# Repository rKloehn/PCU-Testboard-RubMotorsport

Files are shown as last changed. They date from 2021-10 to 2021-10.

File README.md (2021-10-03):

# PCU-Testboard-RubMotorsport

## Overview
The Powertrain Control Board test board (PCU test board for short) was developed in 2020 for the Drivetrain assembly in order to test the functions for the pneumatic switching and coupling of the RUB20 in advance. For this reason, the board contains all the necessary peripherals and connections required for the switching and coupling of the RUB20. The board is supplied with a 12V power supply (like the real PCU in the vehicle). On the board there are connections for two 24V solenoid valves and one proportional valve. Furthermore two sensors with 5V supply voltage each can be connected and the current value of the proportional valve can be read out. For testing the functionality of the switching and coupling process, three push buttons and an adjustment potentiometer are available. All mentioned components were fixed on the board. The control and regulation tasks are performed by a STM32F405RG. The microcontroller can be programmed via the SWD interface on the board. 
<p align="center">
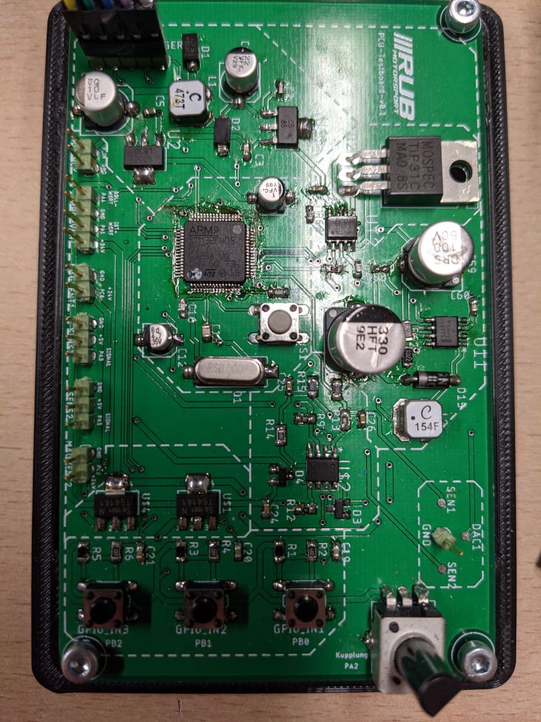
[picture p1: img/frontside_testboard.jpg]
	
</p>

### Sensors
The drivetrain assembly has two sensors specified, which are required for a displacement control of the clutch. A Hall displacement transducer and a pressure sensor are used. The Hall displacement sensor is from the Novotechnik and is sponsored. The sensor is the TFD-4000 series (data sheet TDF-4000). The exact designation of the ordered sensor is: TFD-4021-624-211-401. This sensor has a measuring range of 24mm and a supply voltage of 5V (4.5...5V). The output signal is in the range of 0.25...4.75V and behaves ratiometrically to Ub. The characteristic curve is rising and the sensor is single-channel. Further characteristics can be taken from the data sheet. It is purchased from the company ADZ Nagano. The pressure sensor has a measurable pressure range of FILL IN DATA HERE and requires a supply voltage of 5V. The output signal, similar to the displacement sensor, is ratiometric and is in the range 0.5...4.5V. The sensor has three conductors and a rising characteristic. Further data can be taken from the data sheet (data sheet ADZ-SME).
<p align="center">
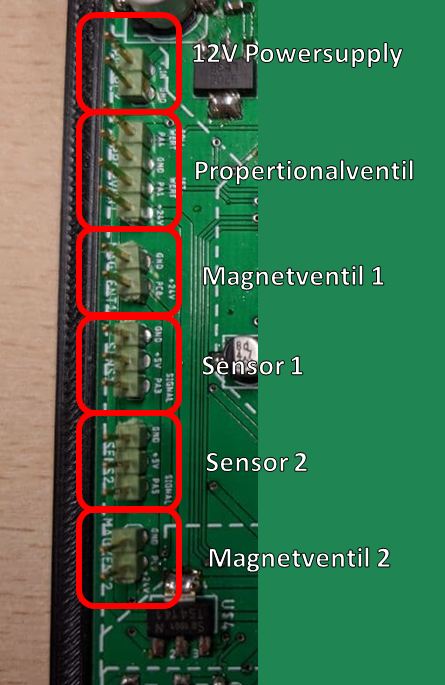
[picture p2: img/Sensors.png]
	
</p>

### Actuators
The actuator system to be controlled by the test board consists of two 24V solenoid valves and one proportional valve. The 24V solenoid valves are from the company FESTO and have the following type description: VUVG-L10-P53E-T-M5_1P3. These are 5/3 [exhausted] valves with a switch-on time of 10ms, a switch-off time of 30ms and a switch-over time of 16ms. The coil is operated with 24V DC with 1W. Further values can be taken from the data sheet (data sheet solenoid valve). The proportional valve is also from the company FESTO and has the type description: VEAA-L-3-D11-Q4-A4-1-R1. The flow valve is controlled by setting the current from 4-20mA. The operating voltage is 24V DC and the electrical connection is a 4-pin M8 connector. Further data can be found in the data sheet.

### User interface
The aim of the test board is to check whether the intended path control and control of the circuit/clutch works. In order for this to happen early in the development process, the board must function completely independently of other boards (e.g. power supply board) or the steering wheel. Thus, it is necessary that the user has a possibility to simulate the actuation of the clutch or the start of a shifting process. For this reason, there are three push buttons on the board, two buttons for upshifting and downshifting and one button for venting the system at the push of a button. A rotary potentiometer also allows the on/off coupling of the motor gearbox. For programming, as mentioned above, the SWD interface is available to the user. The push buttons are all debounced with a corresponding circuit on the board. 

<p align="center">
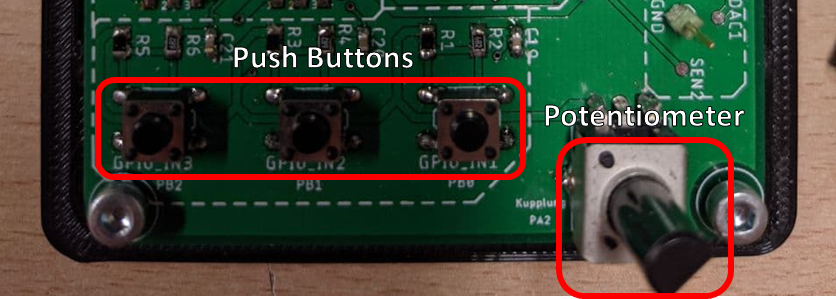
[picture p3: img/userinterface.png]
	
</p>

### Power supply
Several circuits are required for the power supply of the board. In total, exactly three voltage levels are available on the entire PCU test board. The input voltage of the board is 12V DC, which can be provided by a battery or power supply unit. The required current ranges from 0.1A to 0.3A, depending on which peripherals are used. The first voltage level of 5V is achieved by a UA78M05CDCY stepdown converter. The 5V voltage is then either used by the sensors or forms the input voltage for the 5V-3.3V voltage converter. Here a LM2937IMP is used. The 3.3V voltage circuit provides the supply voltage for the microcontroller. The 24V voltage circuit is realized by a StepUp circuit with the MC33063ADG. The 24V are used for the two valves.

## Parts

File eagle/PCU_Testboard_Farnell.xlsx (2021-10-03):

Part Number | Quantity | Description
2146610 | 15 | 100nF 0603
1834255 | 1 | 10µF AlCo 153 CLV 0806
2346907 | 5 | 330nF 0603 50V
2672161 | 5 | 2.2µF 0603 50V
2522596 | 5 | 10000pF 0603 50V
1865475 | 5 | 20pF 0603 50V
2522594 | 5 | 0.1µF 0603 50V
1865487 | 5 | 1500pF 0603 50V
1539494 | 5 | 22µF 0505 35V
1187018 | 5 | 4.7µF 0405 35V
1244367 | 5 | 1µF 0405 25V
2811476 | 5 | 100µF 0810 50V
1299278 | 5 | SK36SMA
2677648 | 5 | SMAJ22
9843671 | 5 | BAS31
1843714 | 5 | 1N5819-B
1829495 | 10 | B3F-1022
2063972 | 1 | FOXSDLF
1652993 | 5 | 39k 0805
1577671 | 5 | 6.8k 0805
2483951 | 5 | 10k 0805
2469524 | 2 | 10k Potentiometer PTV09A-4020F-B103
9294341 | 2 | TIP31C
2215477 | 5 | BTS4141N
1332118 | 5 | MCP6002-E/SN
2296030 | 5 | UA78M05CDCY
3122675 | 5 | LM2937IMP-3.3/NOPB
9664440 | 2 | MC33063ADG
2312176 | 10 | 165 0805
2073658 | 10 | 1.7k 0805
1469911 | 10 | 3.3k 0805
8067600 | 10 | 0.22 0603
1653073 | 10 | 180 0603
1739017 | 10 | 2.2k 0603
2331534 | 10 | 47k 0603
2059432 | 10 | 20k 0603
1692517 | 10 | 100k 0603
2408293 | 2 | 47µH
2408300 | 2 | 150µH LPS6235
1022256 | 10 | Pin8
1868428 | 2 | 330µF 1010

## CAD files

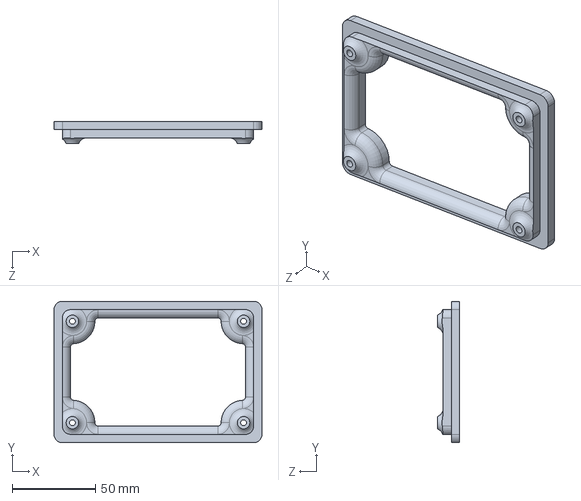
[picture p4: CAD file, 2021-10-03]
eagle/PCU_Testboard_Stand.SLDPRT
125.0 x 85.0 x 13.5 mm

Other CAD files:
eagle/PCU_Testboard_Stand.STL

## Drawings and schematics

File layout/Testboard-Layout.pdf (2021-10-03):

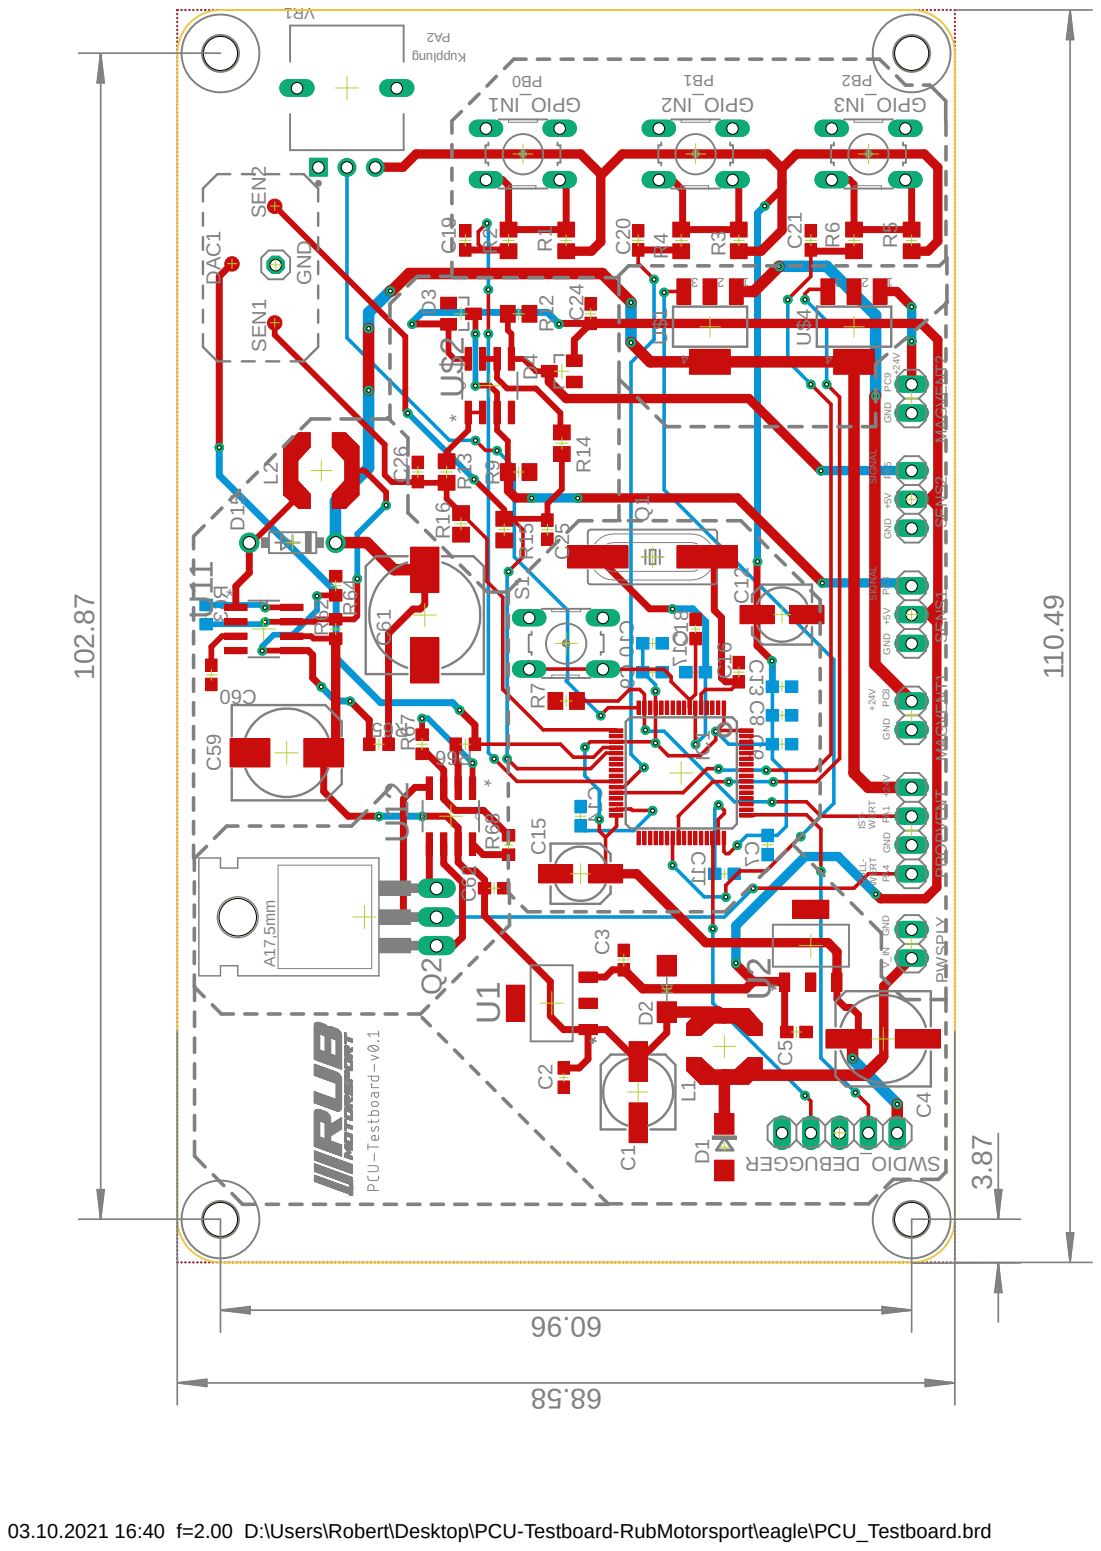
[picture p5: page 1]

* GND V_IN SOLL- WERT GND IST- WERT +24V GND +24V GND GND GND +5V +5V SIGNAL SIGNAL +24V

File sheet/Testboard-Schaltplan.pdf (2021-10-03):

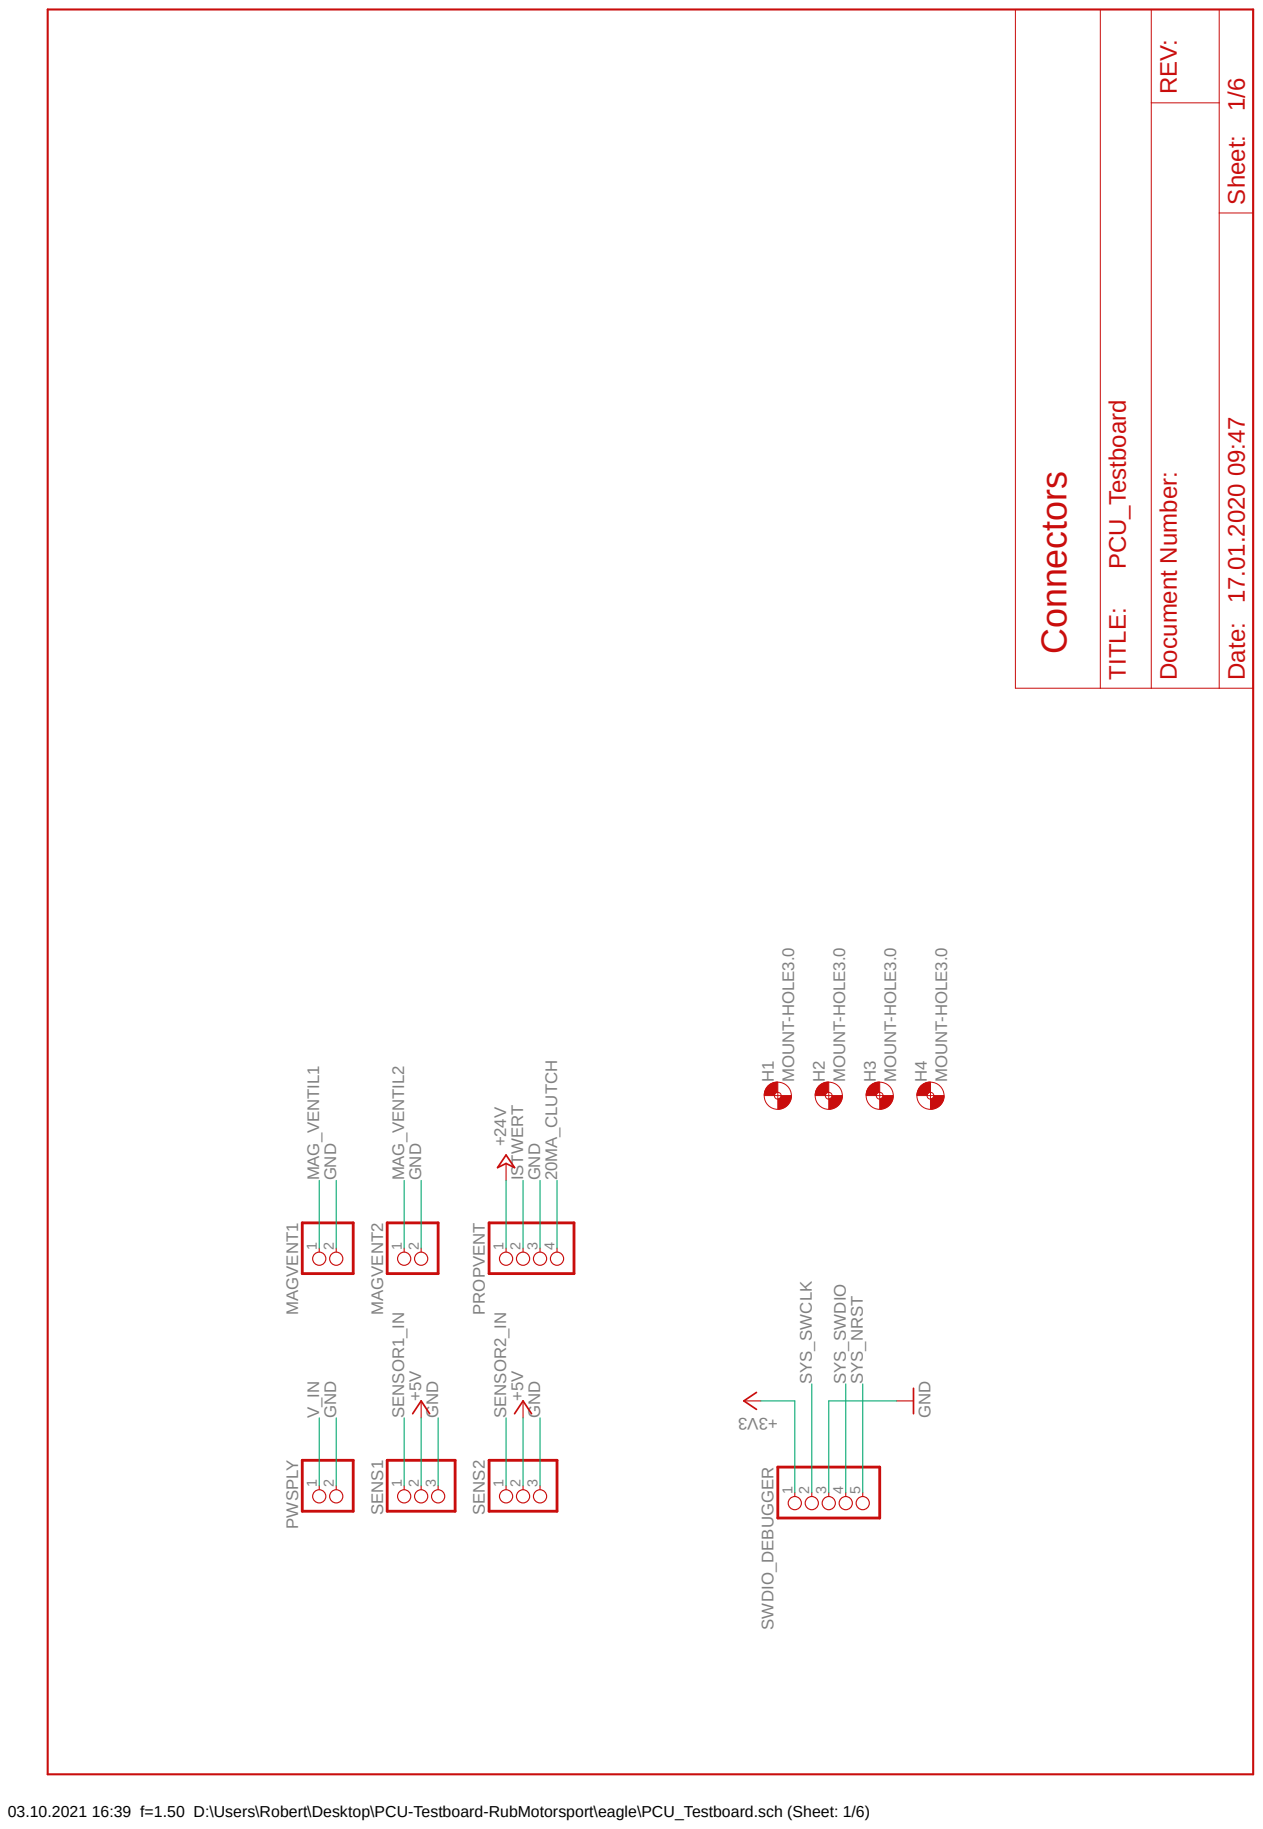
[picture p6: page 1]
5 SWDIO_DEBUGGER1; 2 PWSPLY 1; 3 SENS1; 2 MAGVENT1 1; 2 MAGVENT2; 3 SENS2

4 PROPVENT H1 H2 H3 H4 SYS_SWCLK SYS_SWDIO SYS_NRST GND GND GND GND GND GND V_IN MAG_VENTIL1 MAG_VENTIL2 ISTWERT SENSOR1_IN SENSOR2_IN 20MA_CLUTCH Connectors Date: Sheet: REV: TITLE: Document Number: 17.01.2020 09:47 1/6 PCU_Testboard

03.10.2021 16:39 f=1.50 D:\Users\Robert\Desktop\PCU-Testboard-RubMotorsport\eagle\PCU_Testboard.sch (Sheet: 1/6)

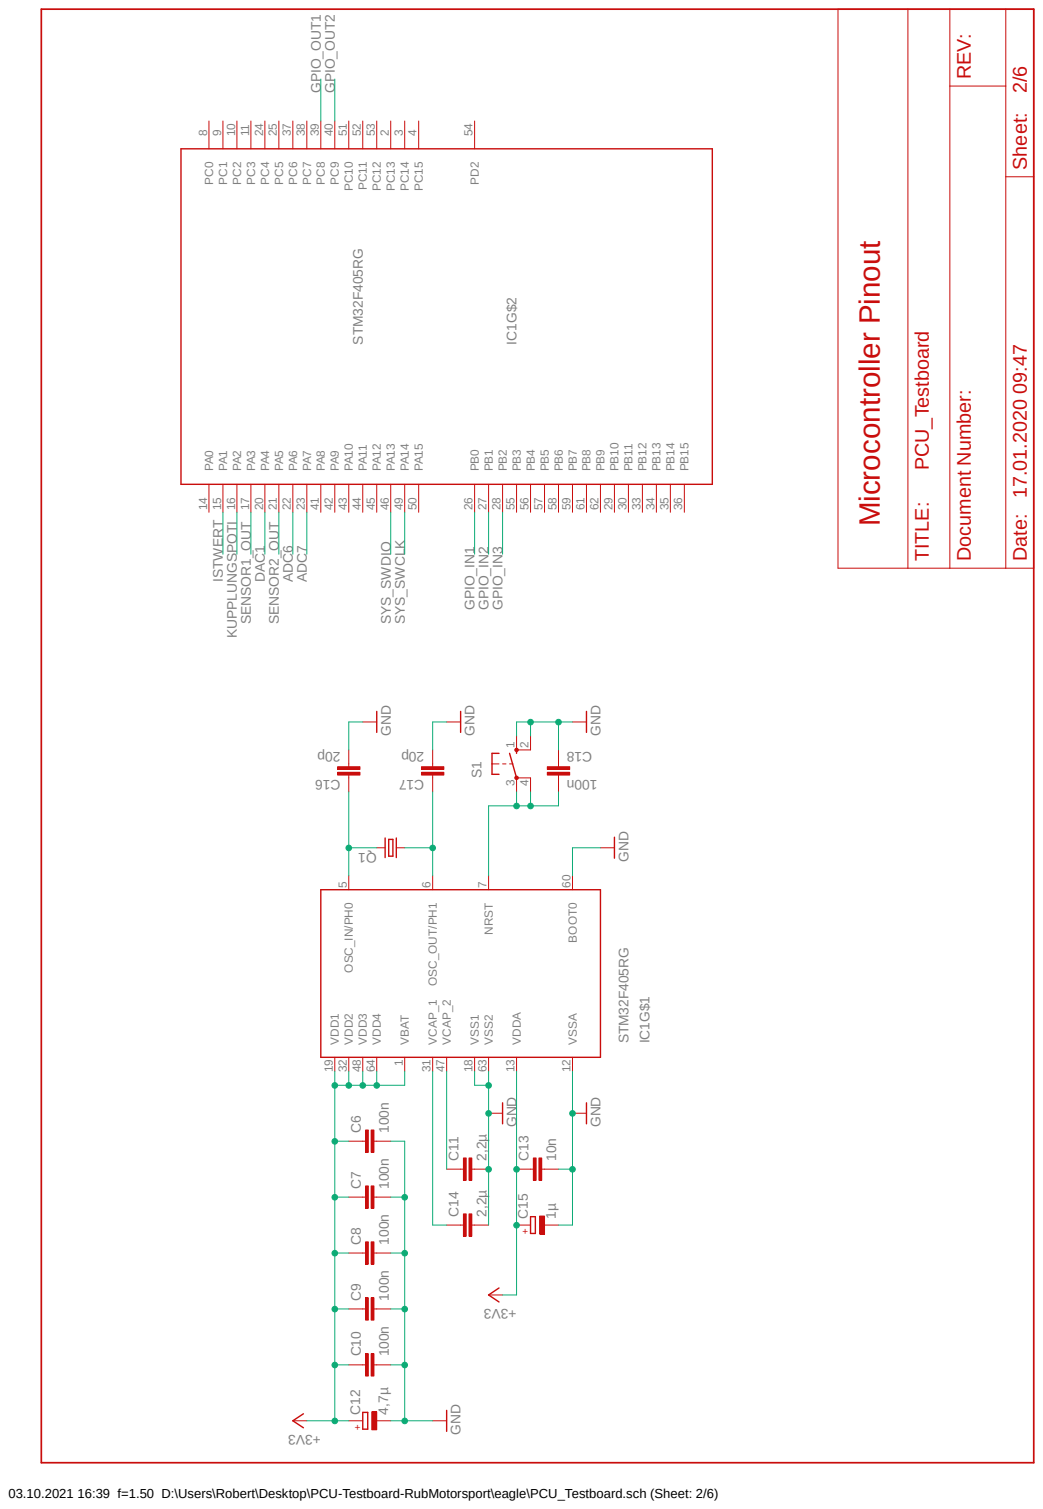
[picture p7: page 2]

C18 SYS_SWDIO SYS_SWCLK GPIO_OUT1 GPIO_OUT2 KUPPLUNGSPOTI SENSOR1_OUT DAC1 SENSOR2_OUT ADC6 ADC7 GPIO_IN1 GPIO_IN2 GPIO_IN3 ISTWERTMicrocontroller Pinout Date: Sheet: REV: TITLE: Document Number: 17.01.2020 09:47 2/6 PCU_Testboard + +

100n GND BOOT0 60 NRST 7 OSC_IN/PH0 5 OSC_OUT/PH1 6 VBAT 1 VCAP_1 31 VCAP_2 47 VDD1 19 VDD2 32 VDD3 48 VDD4 64 VDDA 13 VSS1 18 VSS2 63 VSSA 12 IC1G$1 PA0 14 PA1 15 PA2 16 PA3 17 PA4 20 PA5 21 PA6 22 PA7 23 PA8 41 PA9 42 PA10 43 PA11 44 PA12 45 PA13 46 PA14 49 PA15 50 PB0 26 PB1 27 PB2 28 PB3 55 PB4 56 PB5 57 PB6 58 PB7 59 PB8 61 PB9 62 PB10 29 PB11 30 PB12 33 PB13 34 PB14 35 PB15 36 PC0 8 PC1 9 PC2 10 PC3 11 PC4 24 PC5 25 PC6 37 PC7 38 PC8 39 PC9 40 PC10 51 PC11 52 PC12 53 PC13 2 PC14 3 PC15 4 PD2 54 IC1G$2 C6 C7 C8 C9 C10 C12 C11 C14 C13 C15

03.10.2021 16:39 f=1.50 D:\Users\Robert\Desktop\PCU-Testboard-RubMotorsport\eagle\PCU_Testboard.sch (Sheet: 2/6) STM³²F405RG STM³²F405RG 100n 100n 100n 100n 100n 4,7µ

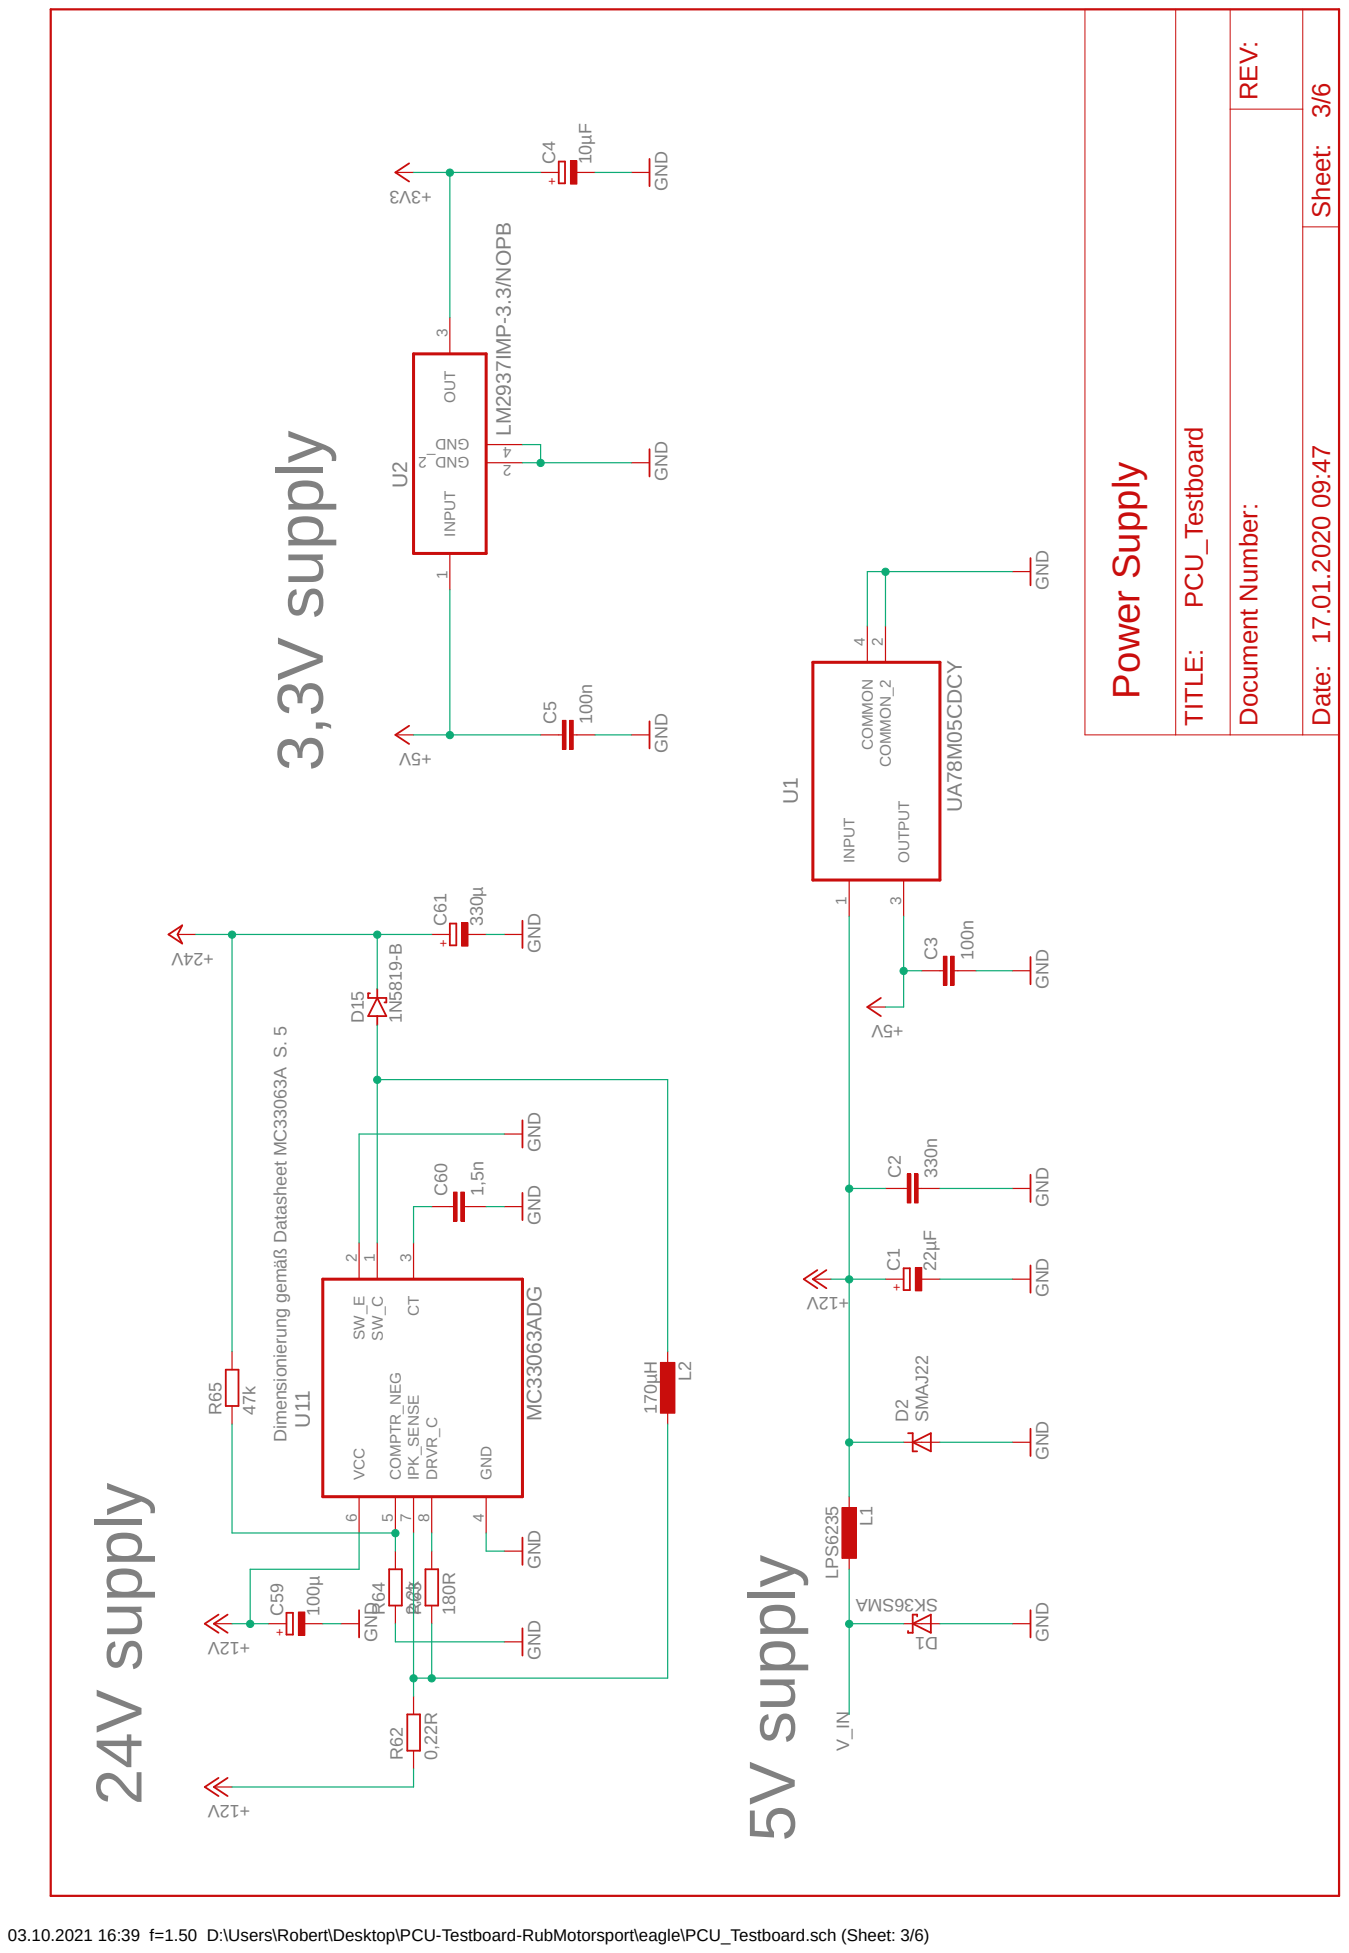
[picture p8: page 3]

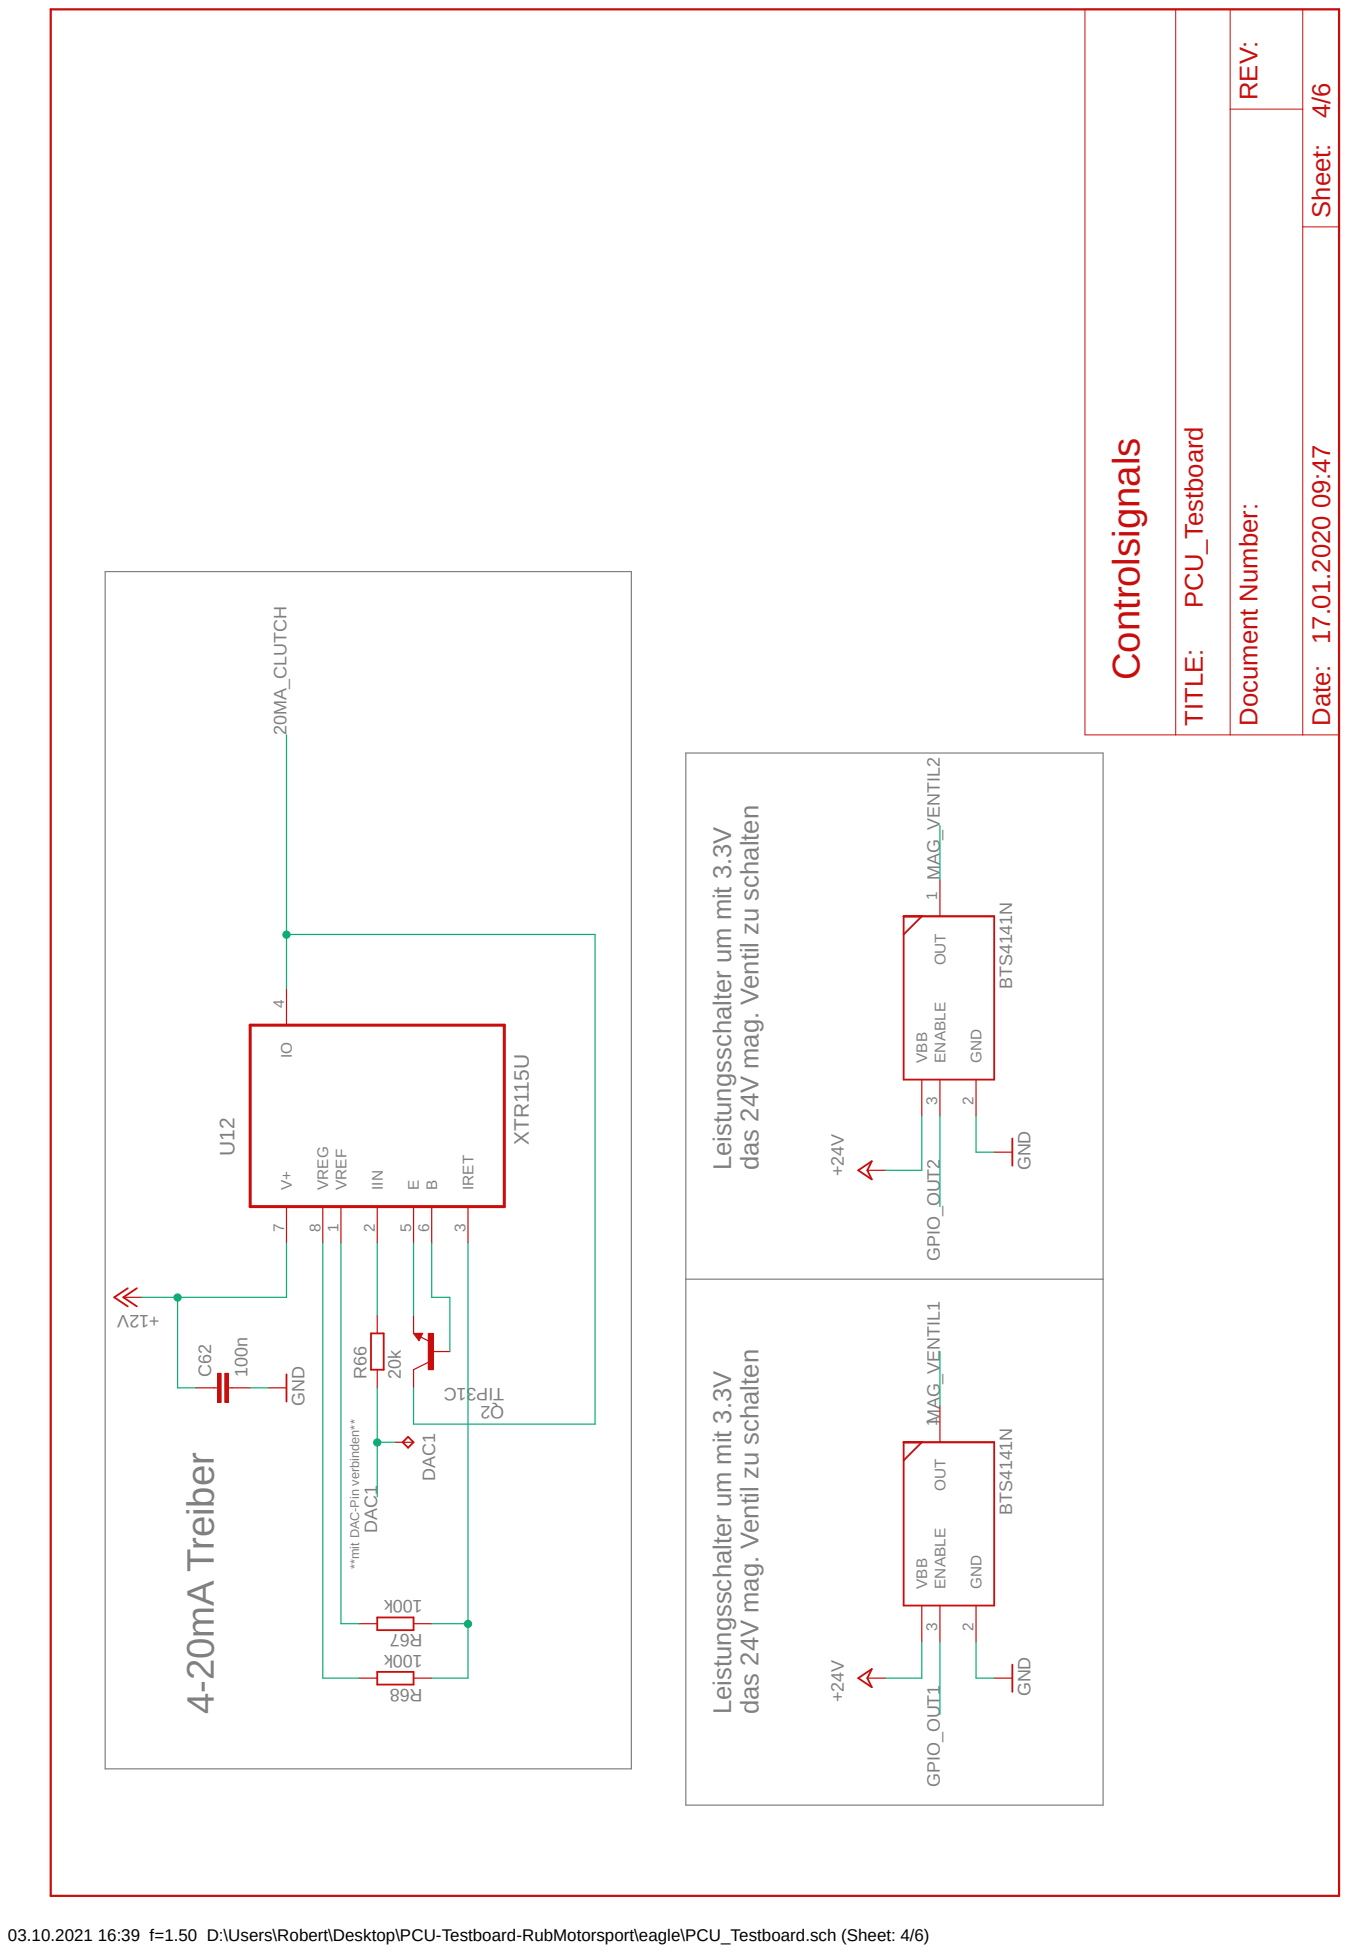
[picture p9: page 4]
03.10.2021 16:39 f=1.50 D:\Users\Robert\Desktop\PCU-Testboard-RubMotorsport\eagle\PCU_Testboard.sch (Sheet: 4/6) **mit DAC⁻Pin verbinden** 4⁻20mA Treiber; Leistungsschalter um mit 3.3V das 24V mag. Ventil zu schalten Leistungsschalter um mit 3.3V das 24V mag. Ventil zu schalten; BTS⁴¹⁴¹N BTS⁴¹⁴¹N XTR¹¹⁵U 20k; 7 VREG 8 VREF; 1 IIN 2 E; 6 IRET; 3 GND; 2 OUT; 1 VBB ENABLE

1 DAC1 DAC1 20MA_CLUTCH GPIO_OUT1 MAG_VENTIL1 MAG_VENTIL2 GPIO_OUT2 Controlsignals Date: Sheet: REV: TITLE: Document Number: 17.01.2020 09:47 4/6 PCU_Testboard

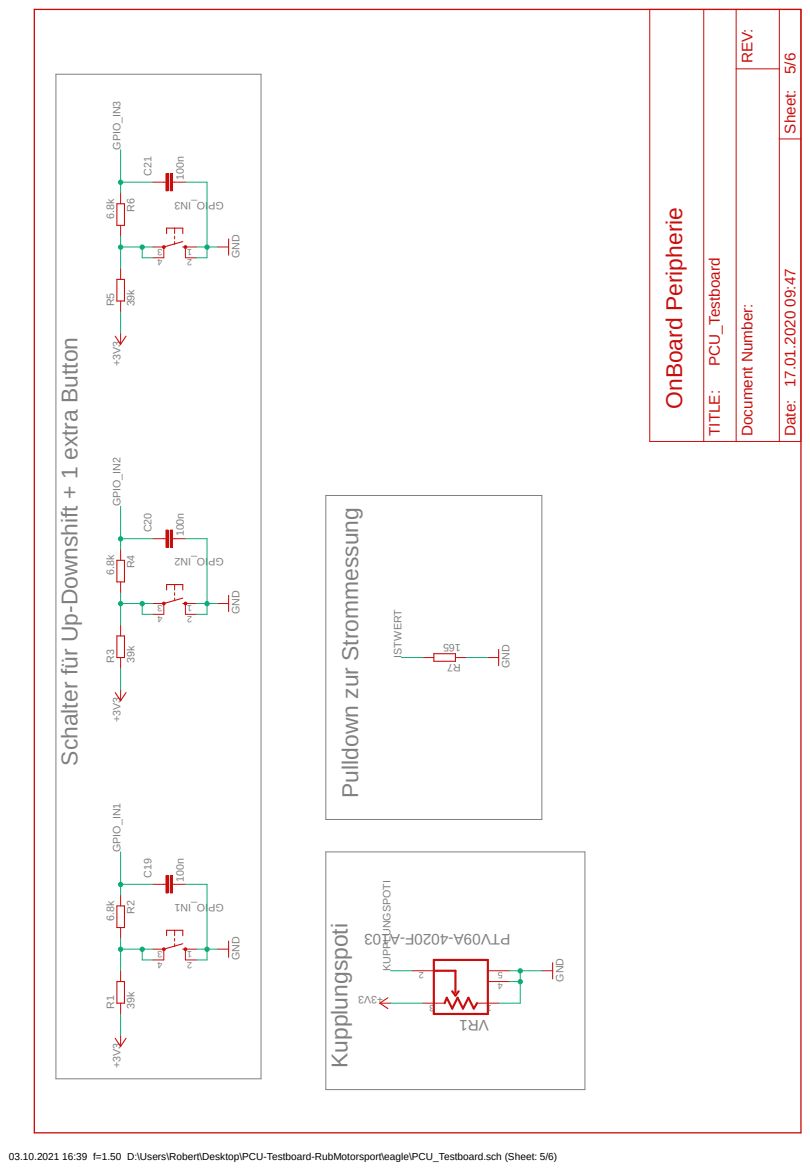
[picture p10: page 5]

VR1 GPIO_IN1 GPIO_IN2 GPIO_IN3 KUPPLUNGSPOTI ISTWERT OnBoard Peripherie Date: Sheet: REV: TITLE: Document Number: 17.01.2020 09:47 5/6 PCU_Testboard

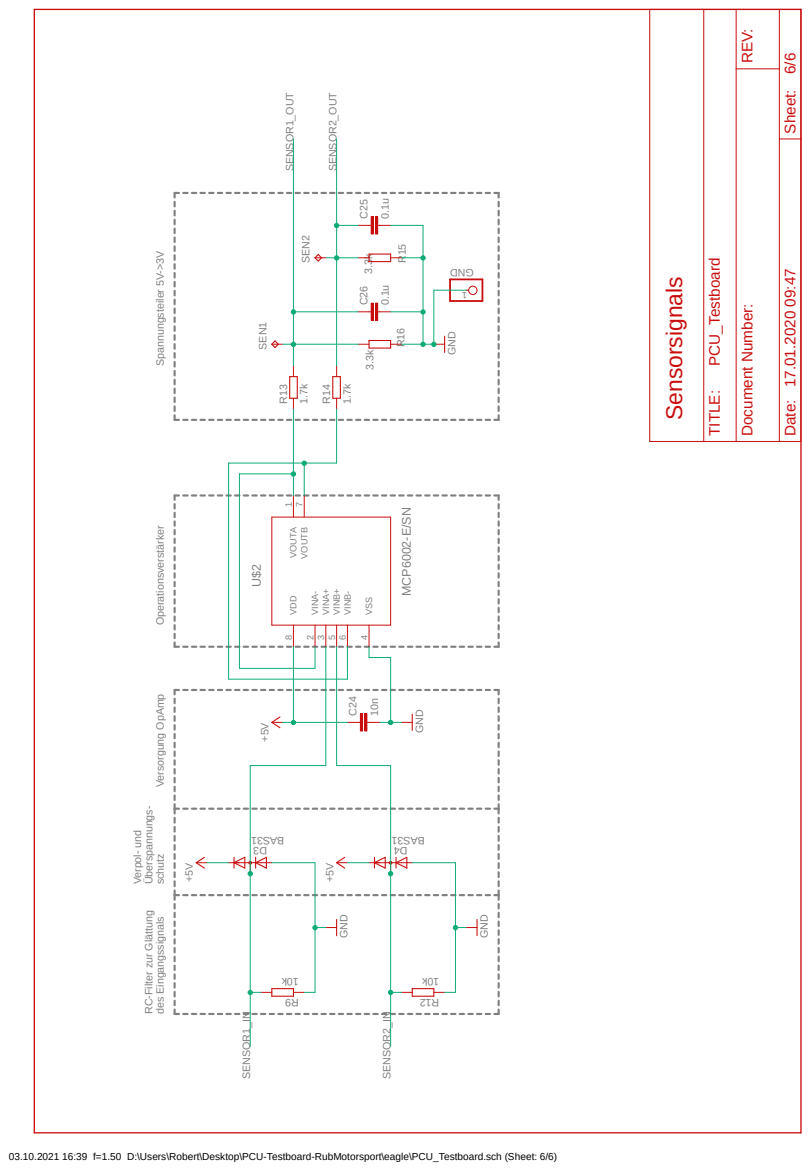
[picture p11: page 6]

GND SENSOR1_IN SENSOR2_IN SENSOR1_OUT SENSOR2_OUT Sensorsignals Date: Sheet: REV: TITLE: Document Number: 17.01.2020 09:47 6/6 PCU_Testboard

10k +5V 10n GND 1.7k 1.7k 3.3k 3.3k 0.1u 0.1u GND VDD 8 VINA- 2 VINA+ 3 VINB+ 5 VINB- 6 VSS 4 VOUTA 1 VOUTB 7 U$2

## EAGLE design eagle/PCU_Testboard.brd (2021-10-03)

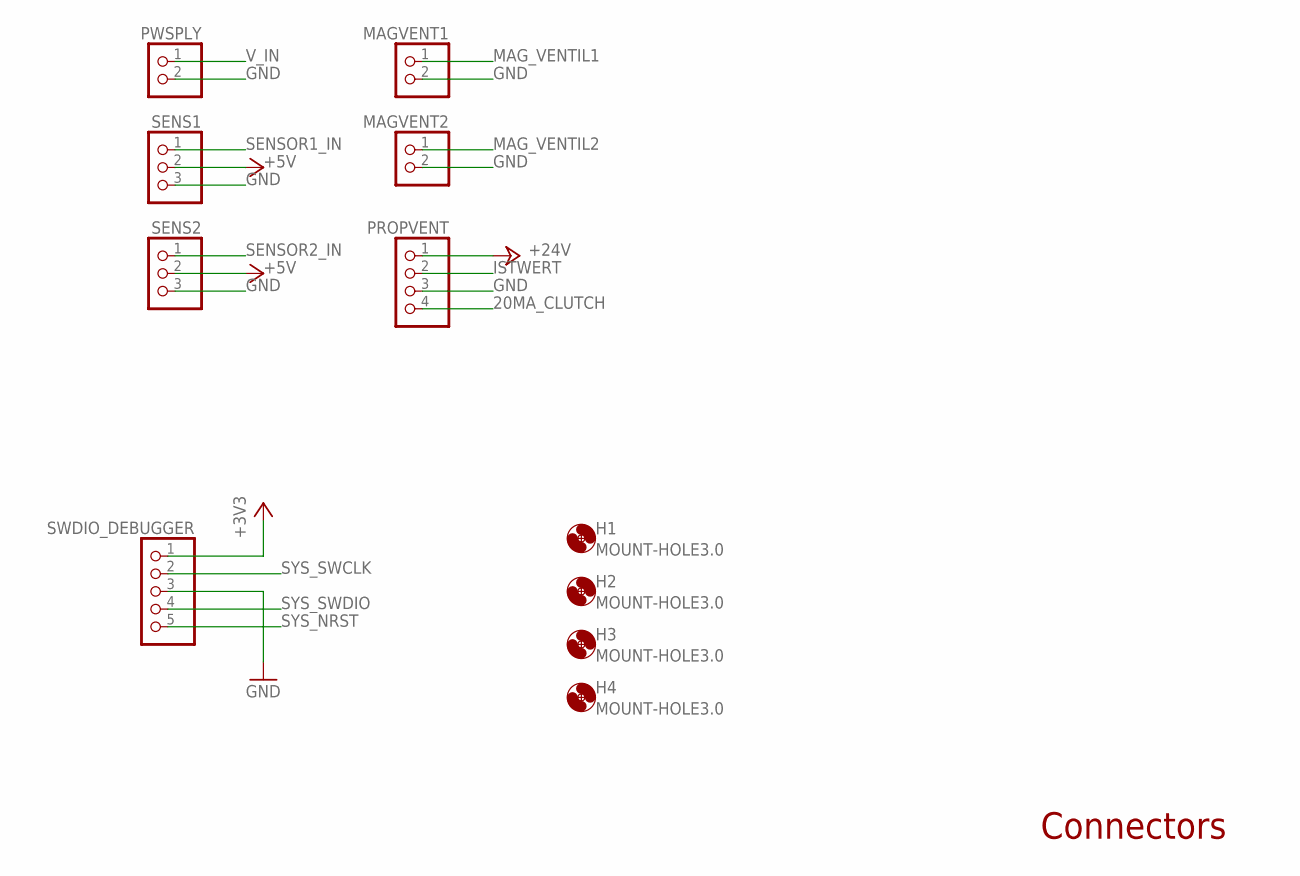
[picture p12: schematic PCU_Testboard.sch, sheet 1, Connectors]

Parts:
H1, H2, H3, H4: MOUNT-HOLE3.0; 3,0
MAGVENT1, MAGVENT2: PINHD-1X2; 1X02
PROPVENT: PINHD-1X4; 1X04
PWSPLY: PINHD-1X2; 1X02
SENS1, SENS2: PINHD-1X3; 1X03
SWDIO_DEBUGGER: PINHD-1X5; 1X05

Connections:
20MA_CLUTCH: PROPVENT.4; also elsewhere on the board
+3V3: SWDIO_DEBUGGER.1; also elsewhere on the board
+5V: SENS1.2, SENS2.2; also elsewhere on the board
+24V: PROPVENT.1; also elsewhere on the board
GND: MAGVENT1.2, MAGVENT2.2, PROPVENT.3, PWSPLY.2, SENS1.3, SENS2.3, SWDIO_DEBUGGER.3; also elsewhere on the board
ISTWERT: PROPVENT.2; also elsewhere on the board
MAG_VENTIL1: MAGVENT1.1; also elsewhere on the board
MAG_VENTIL2: MAGVENT2.1; also elsewhere on the board
SENSOR1_IN: SENS1.1; also elsewhere on the board
SENSOR2_IN: SENS2.1; also elsewhere on the board
SYS_NRST: SWDIO_DEBUGGER.5
SYS_SWCLK: SWDIO_DEBUGGER.2; also elsewhere on the board
SYS_SWDIO: SWDIO_DEBUGGER.4; also elsewhere on the board
V_IN: PWSPLY.1; also elsewhere on the board

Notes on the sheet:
Connectors

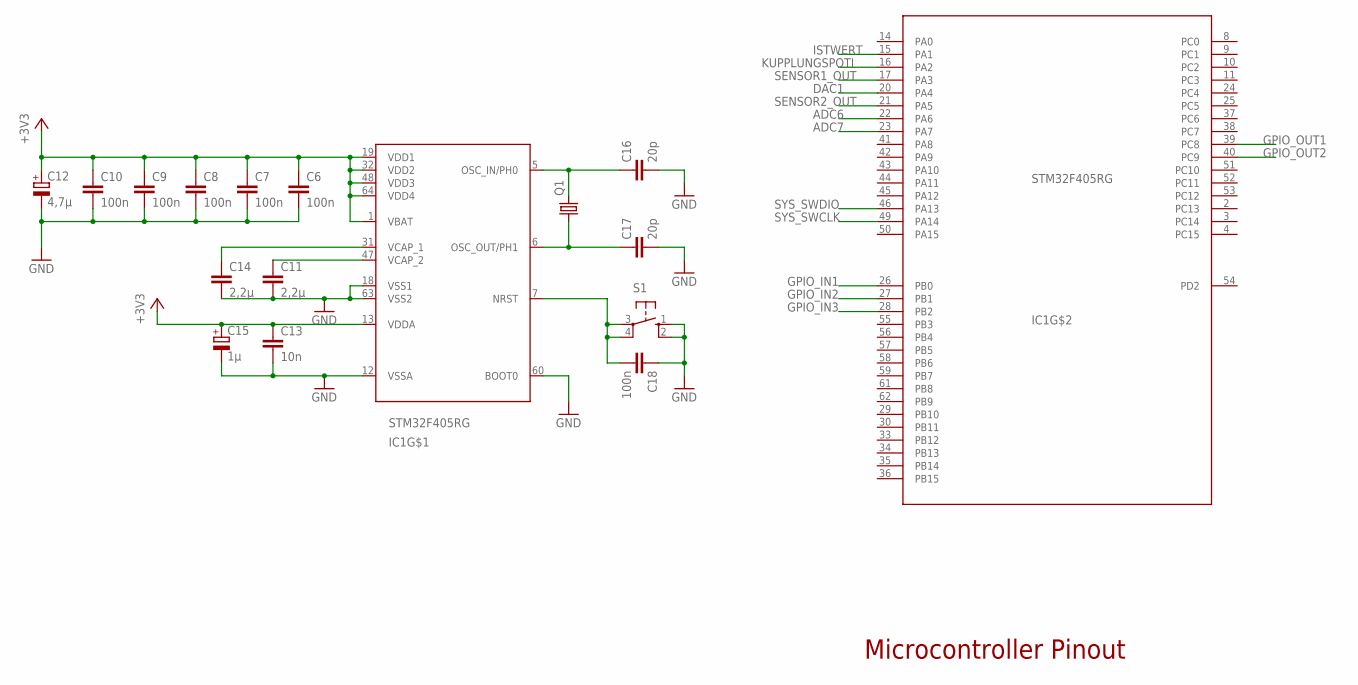
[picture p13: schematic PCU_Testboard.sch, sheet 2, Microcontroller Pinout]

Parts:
C6, C7, C8, C9, C10, C18: 100n; C0603
C11, C14: 2,2µ; C0603
C12: 4,7µ; 153CLV-0505
C13: 10n; C0603
C15: 1µ; 153CLV-0505
C16, C17: 20p; C0603
IC1: STM32F405RG; LQFP64
Q1: CRYSTALHC49UP; HC49UP
S1: 10-XX; B3F-10XX

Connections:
+3V3: C6.1, C7.1, C8.1, C9.1, C10.1, C12.+, C13.1, C15.+, IC1.1 (VBAT), IC1.13 (VDDA), IC1.19 (VDD1), IC1.32 (VDD2), IC1.48 (VDD3), IC1.64 (VDD4); also elsewhere on the board
ADC6: IC1.22 (PA6)
ADC7: IC1.23 (PA7)
DAC1: IC1.20 (PA4); also elsewhere on the board
GND: C6.2, C7.2, C8.2, C9.2, C10.2, C11.2, C12.-, C13.2, C14.2, C15.-, C16.2, C17.2, C18.1, IC1.12 (VSSA), IC1.18 (VSS1), IC1.60 (BOOT0), IC1.63 (VSS2), S1.1 (S), S1.2 (S1); also elsewhere on the board
GPIO_IN1: IC1.26 (PB0); also elsewhere on the board
GPIO_IN2: IC1.27 (PB1); also elsewhere on the board
GPIO_IN3: IC1.28 (PB2); also elsewhere on the board
GPIO_OUT1: IC1.39 (PC8); also elsewhere on the board
GPIO_OUT2: IC1.40 (PC9); also elsewhere on the board
ISTWERT: IC1.15 (PA1); also elsewhere on the board
KUPPLUNGSPOTI: IC1.16 (PA2); also elsewhere on the board
unnamed: C14.1, IC1.31 (VCAP_1)
unnamed: C11.1, IC1.47 (VCAP_2)
unnamed: C16.1, IC1.5 (OSC_IN/PH0), Q1.2
unnamed: C17.1, IC1.6 (OSC_OUT/PH1), Q1.1
unnamed: C18.2, IC1.7 (NRST), S1.3, S1.4 (P1)
SENSOR1_OUT: IC1.17 (PA3); also elsewhere on the board
SENSOR2_OUT: IC1.21 (PA5); also elsewhere on the board
SYS_SWCLK: IC1.49 (PA14); also elsewhere on the board
SYS_SWDIO: IC1.46 (PA13); also elsewhere on the board

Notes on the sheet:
Microcontroller Pinout

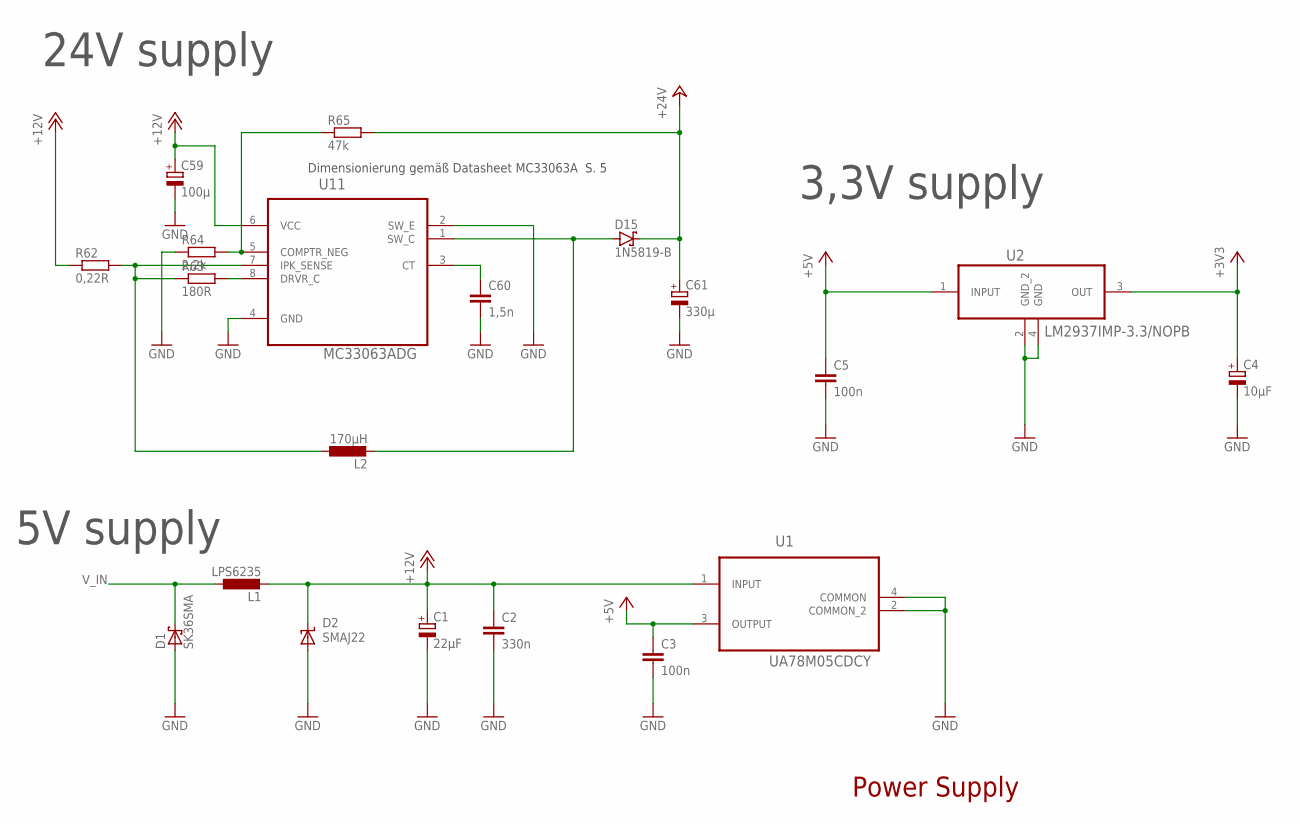
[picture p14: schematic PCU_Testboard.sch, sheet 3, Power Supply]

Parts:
C1: 22µF; 153CLV-0605
C2: 330n; C0603
C3, C5: 100n; C0603
C4: 10µF; 153CLV-0807
C59: 100µ; 150CLZ-0810
C60: 1,5n; C0603
C61: 330µ; 153CLV-1010
D1: SK36SMA; DO214AC
D2: SMAJ22; SMA-DO214AC
D15: 1N5819-B; DO41-7.6
L1: LPS6235
L2: 170µH; LPS6235
R62: 0,22R; R0603
R63: 180R; R0603
R64: 2,2k; R0603
R65: 47k; R0603
U1: UA78M05CDCY; SOT230P700X180-4N
U2: LM2937IMP-3.3/NOPB; SOT230P700X180-4N
U11: MC33063ADG; SOIC127P600X175-8N

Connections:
+3V3: C4.+, U2.3 (OUT); also elsewhere on the board
+5V: C3.1, C5.1, U1.3 (OUTPUT), U2.1 (INPUT); also elsewhere on the board
+12V: C1.+, C2.1, C59.+, D2.K (C), L1.2, R62.1, U1.1 (INPUT), U11.6 (VCC); also elsewhere on the board
+24V: C61.+, D15.C, R65.2; also elsewhere on the board
GND: C1.-, C2.2, C3.2, C4.-, C5.2, C59.-, C60.2, C61.-, D1.A, D2.A, R64.1, U1.2 (COMMON_2), U1.4 (COMMON), U2.2 (GND_2), U2.4 (GND), U11.2 (SW_E), U11.4 (GND); also elsewhere on the board
unnamed: C60.1, U11.3 (CT)
unnamed: L2.1, R62.2, R63.1, U11.7 (IPK_SENSE)
unnamed: R63.2, U11.8 (DRVR_C)
unnamed: D15.A, L2.2, U11.1 (SW_C)
unnamed: R64.2, R65.1, U11.5 (COMPTR_NEG)
V_IN: D1.C, L1.1; also elsewhere on the board

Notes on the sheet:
Dimensionierung gemäß Datasheet MC33063A S. 5
24V supply
3,3V supply
5V supply
Power Supply

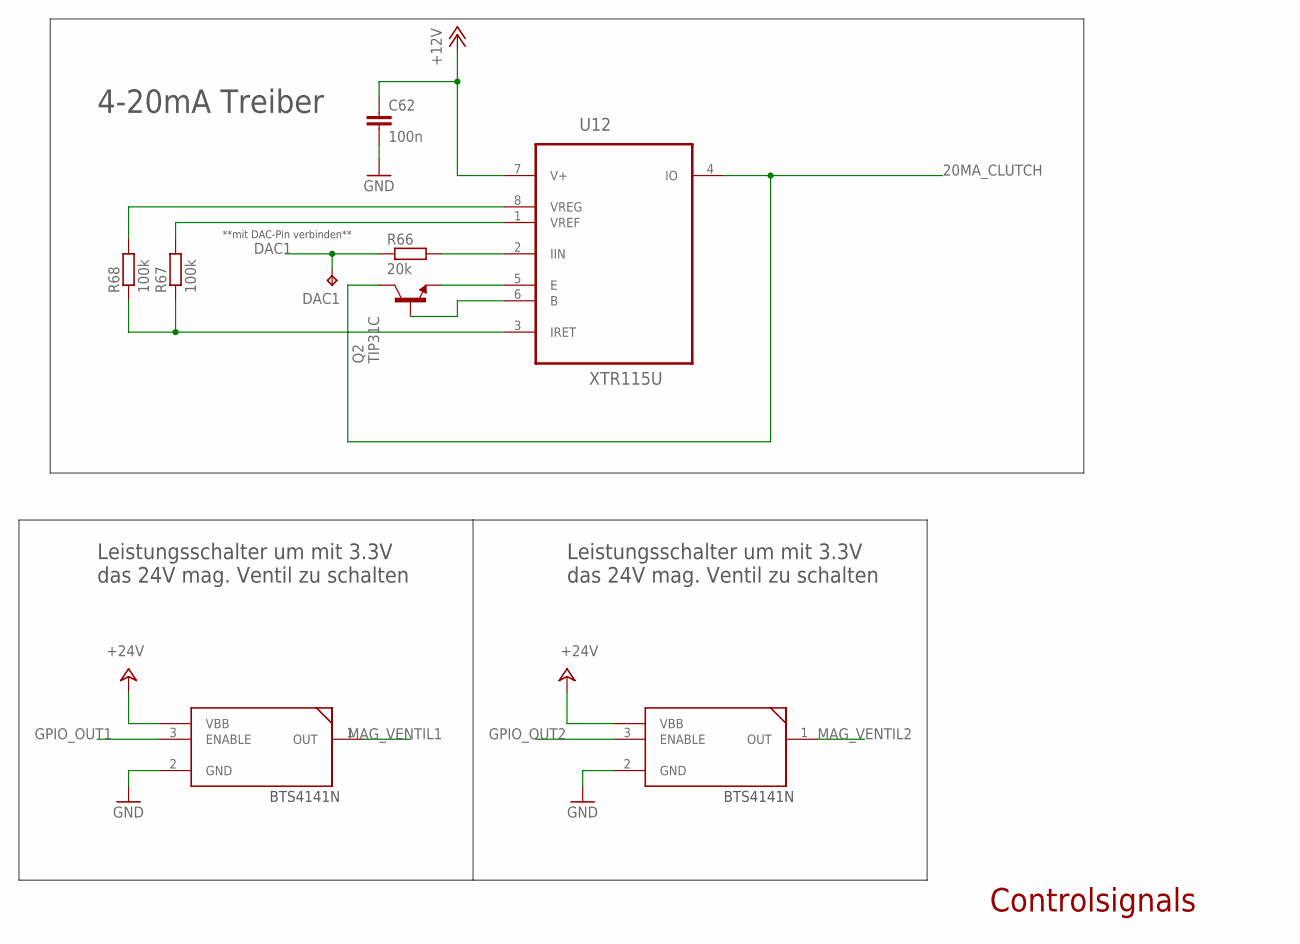
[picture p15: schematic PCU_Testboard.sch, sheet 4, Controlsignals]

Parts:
C62: 100n; C0603
DAC1: TPB1,27; B1,27
Q2: TIP31C; TO220
R66: 20k; R0603
R67, R68: 100k; R0603
U12: XTR115U; SOIC127P600X175-8N
U$1, U$4: BTS4141N; SOT223

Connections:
20MA_CLUTCH: Q2.2 (C), U12.4 (IO); also elsewhere on the board
+12V: C62.1, U12.7 (V+); also elsewhere on the board
+24V: U$1.4 (VBB), U$4.4 (VBB); also elsewhere on the board
DAC1: DAC1.TP, R66.1; also elsewhere on the board
GND: C62.2, U$1.2 (GND), U$4.2 (GND); also elsewhere on the board
GPIO_OUT1: U$1.3 (ENABLE); also elsewhere on the board
GPIO_OUT2: U$4.3 (ENABLE); also elsewhere on the board
MAG_VENTIL1: U$1.1 (OUT); also elsewhere on the board
MAG_VENTIL2: U$4.1 (OUT); also elsewhere on the board
unnamed: R66.2, U12.2 (IIN)
unnamed: Q2.3 (E), U12.5 (E)
unnamed: Q2.1 (B), U12.6 (B)
unnamed: R67.2, U12.1 (VREF)
unnamed: R68.2, U12.8 (VREG)
unnamed: R67.1, R68.1, U12.3 (IRET)

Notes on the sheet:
**mit DAC-Pin verbinden**
4-20mA Treiber
Controlsignals
Leistungsschalter um mit 3.3V das 24V mag. Ventil zu schalten

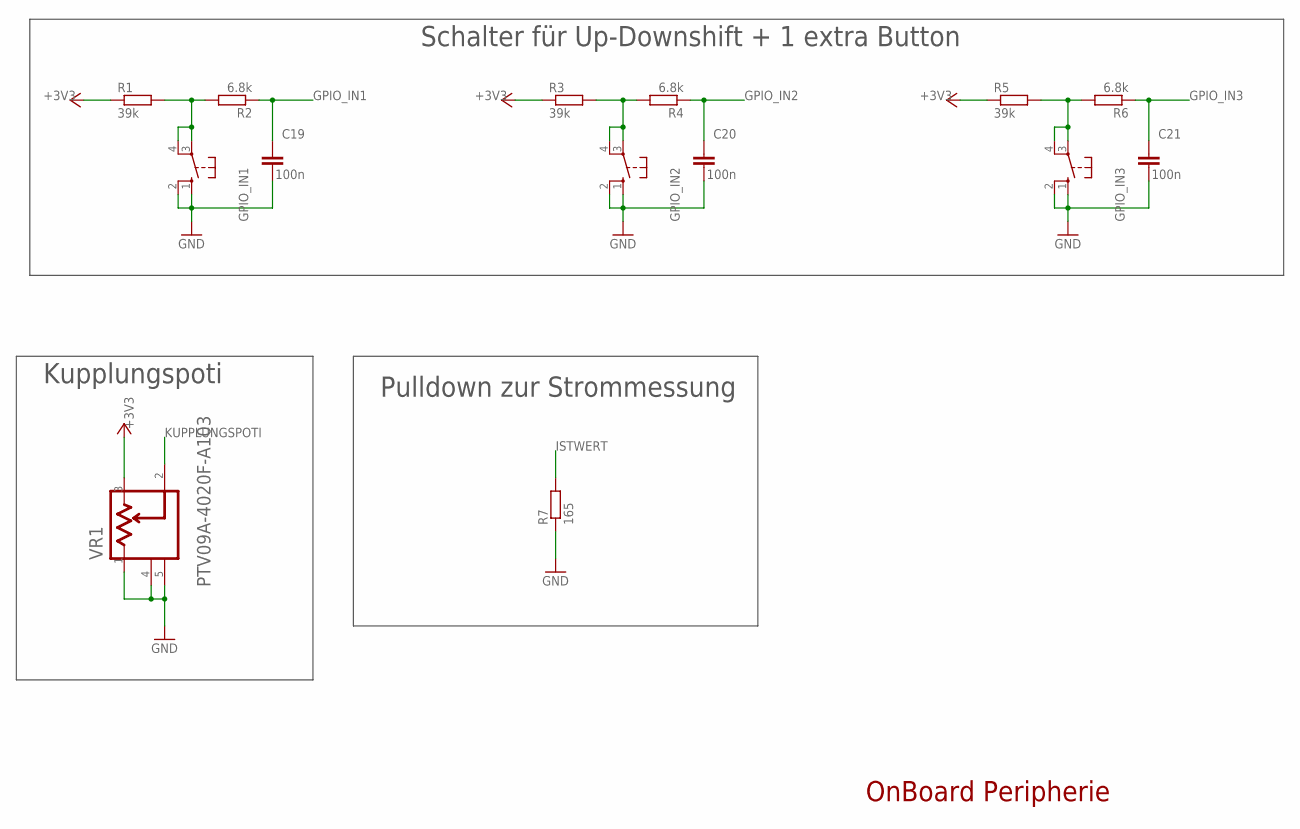
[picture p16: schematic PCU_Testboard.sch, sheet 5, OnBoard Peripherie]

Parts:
C19, C20, C21: 100n; C0603
GPIO_IN1, GPIO_IN2, GPIO_IN3: 10-XX; B3F-10XX
R1, R3, R5: 39k; R0805
R2, R4, R6: 6.8k; R0805
R7: 165; R0805
VR1: BOURNS_PTV09A-4020F-A103BOURNS_PTV09A-4020F-A103_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; BOURNS_PTV09A-4020F-A103_0

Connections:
+3V3: R1.1, R3.1, R5.1, VR1.3; also elsewhere on the board
GND: C19.2, C20.2, C21.2, GPIO_IN1.1 (S), GPIO_IN1.2 (S1), GPIO_IN2.1 (S), GPIO_IN2.2 (S1), GPIO_IN3.1 (S), GPIO_IN3.2 (S1), R7.1, VR1.1, VR1.4 (MNT_1), VR1.5 (MNT_2); also elsewhere on the board
GPIO_IN1: C19.1, R2.1; also elsewhere on the board
GPIO_IN2: C20.1, R4.1; also elsewhere on the board
GPIO_IN3: C21.1, R6.1; also elsewhere on the board
ISTWERT: R7.2; also elsewhere on the board
KUPPLUNGSPOTI: VR1.2; also elsewhere on the board
unnamed: GPIO_IN1.3, GPIO_IN1.4 (P1), R1.2, R2.2
unnamed: GPIO_IN2.3, GPIO_IN2.4 (P1), R3.2, R4.2
unnamed: GPIO_IN3.3, GPIO_IN3.4 (P1), R5.2, R6.2

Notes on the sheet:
OnBoard Peripherie
Schalter für Up-Downshift + 1 extra Button
Pulldown zur Strommessung
Kupplungspoti

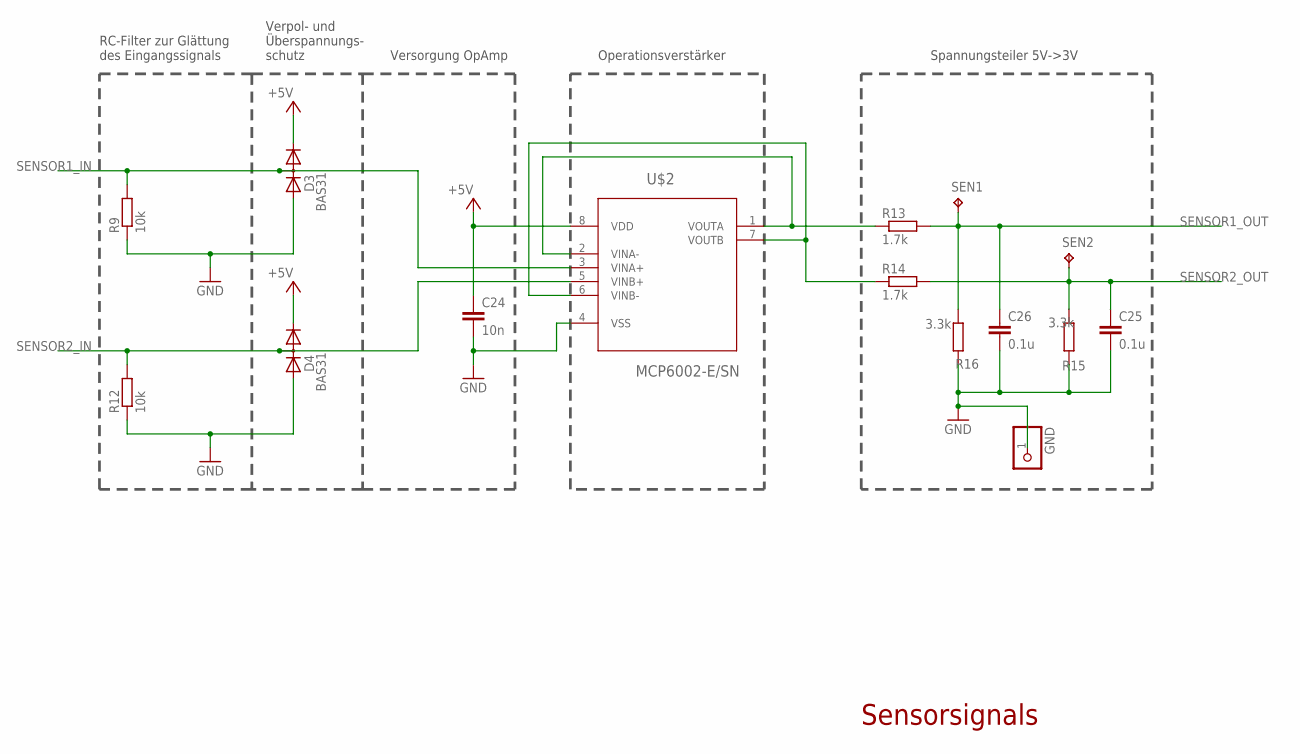
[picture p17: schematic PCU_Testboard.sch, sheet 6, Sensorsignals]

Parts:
C24: 10n; C0603
C25, C26: 0.1u; C0603
D3, D4: BAS31; SOT23
GND: PINHD-1X1; 1X01
R9, R12: 10k; R0805
R13, R14: 1.7k; R0805
R15, R16: 3.3k; R0805
SEN1, SEN2: TPB1,27; B1,27
U$2: MCP6002-E/SN; SOIC127P600X175-8N

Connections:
+5V: C24.1, D3.2 (C), D4.2 (C), U$2.8 (VDD); also elsewhere on the board
GND: C24.2, C25.2, C26.2, D3.1 (A), D4.1 (A), GND.1, R9.1, R12.1, R15.2, R16.1, U$2.4 (VSS); also elsewhere on the board
unnamed: R13.1, U$2.1 (VOUTA), U$2.2 (VINA-)
unnamed: R14.1, U$2.6 (VINB-), U$2.7 (VOUTB)
SENSOR1_IN: D3.3 (AC), R9.2, U$2.3 (VINA+); also elsewhere on the board
SENSOR1_OUT: C26.1, R13.2, R16.2, SEN1.TP; also elsewhere on the board
SENSOR2_IN: D4.3 (AC), R12.2, U$2.5 (VINB+); also elsewhere on the board
SENSOR2_OUT: C25.1, R14.2, R15.1, SEN2.TP; also elsewhere on the board

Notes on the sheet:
RC-Filter zur Glättung des Eingangssignals
Verpol- und Überspannungs- schutz
Versorgung OpAmp
Spannungsteiler 5V->3V
Operationsverstärker
Sensorsignals

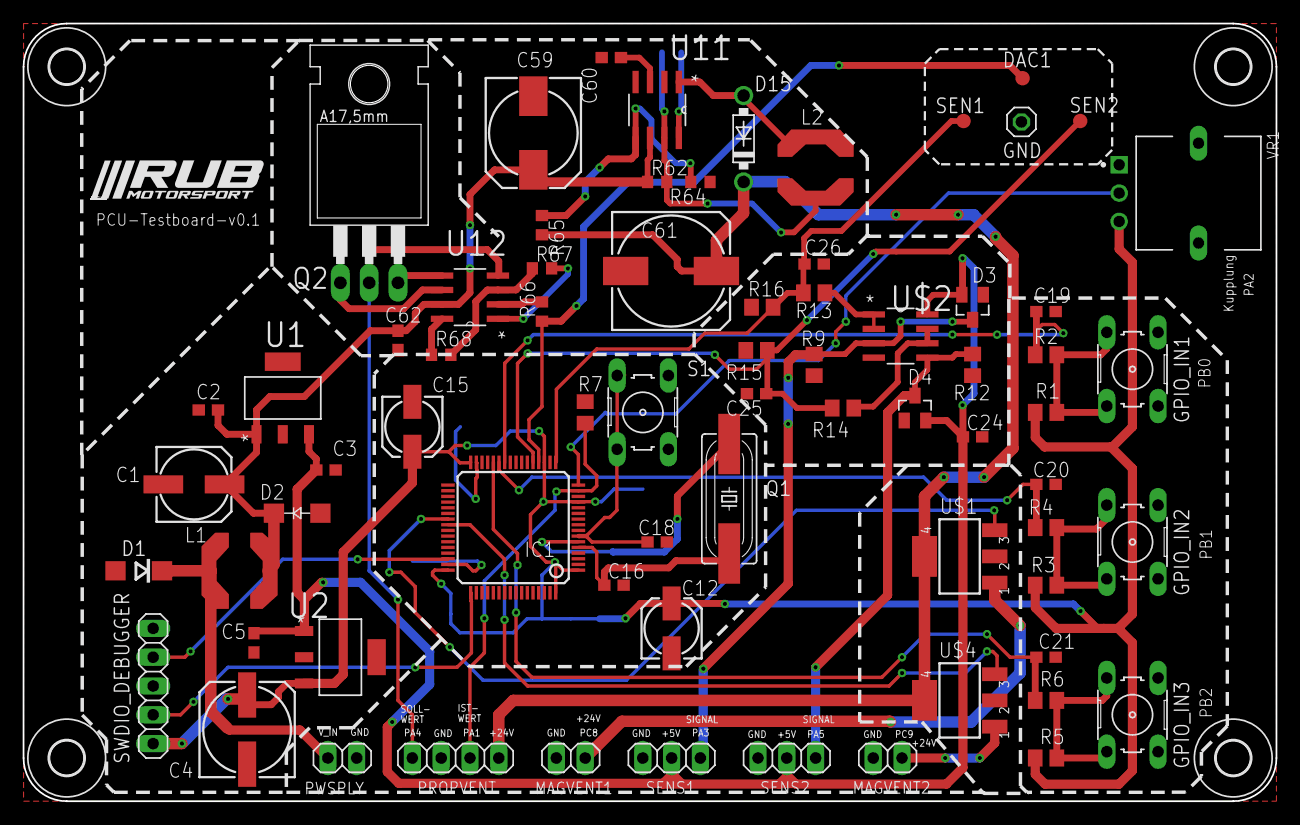
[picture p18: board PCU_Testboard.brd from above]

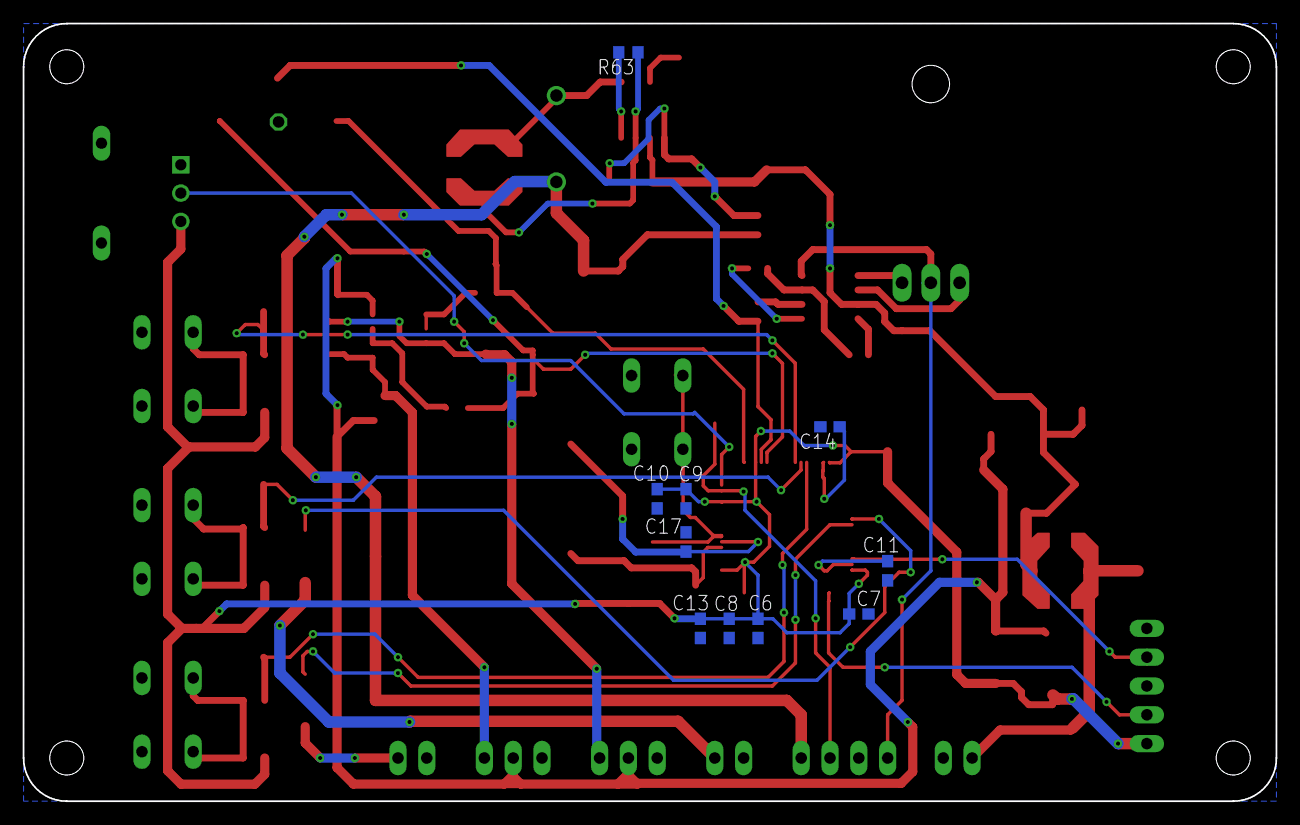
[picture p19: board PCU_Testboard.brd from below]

Board: 2 copper layers, 110.5 x 68.6 mm, 85 parts (10 on the bottom side), 44 nets.
